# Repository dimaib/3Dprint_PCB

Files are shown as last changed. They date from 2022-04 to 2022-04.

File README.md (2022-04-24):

# 3D printer Dual
## Description
A board for controlling all parts of a dual-extruder 3D printer.
- Allows you to control 6 stepper motors
- Table heating 110-230V
- Chamber heating 110-230V
- Heat control of two extruders
- Connection of various limit switches
- Connecting the LCD display
- Printer management via web interface via TCP/IP
>This board is controlled by [RepRapFirmware](https://reprap.org/wiki/RepRap_Firmware) ([GitHub](https://github.com/reprappro/RepRapFirmware))

RepRapFirmware has been optimized and redesigned for the STM32F407VGT controller architecture

## Tools and softwire
- The printed circuit board and circuit diagram of the device are created in [KiCad](https://www.kicad.org/)
- 3D models for PCB components were created in SOLIDWORKS
- Firmware edit in [Atollic TrueSTUDIO for STM32](https://www.st.com/en/development-tools/truestudio.html) in C languages
## Main view PCB
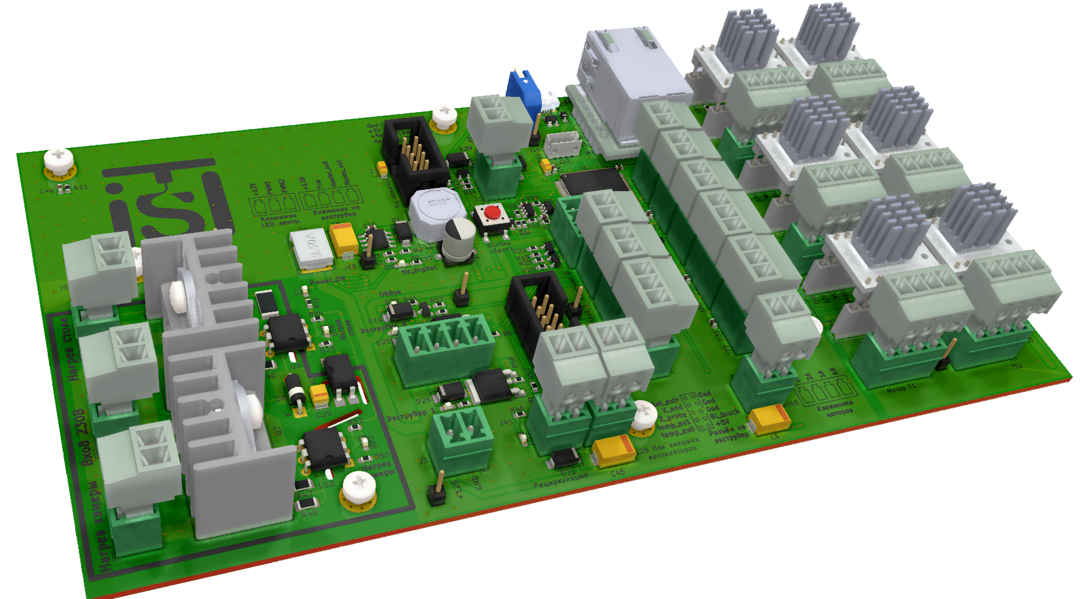
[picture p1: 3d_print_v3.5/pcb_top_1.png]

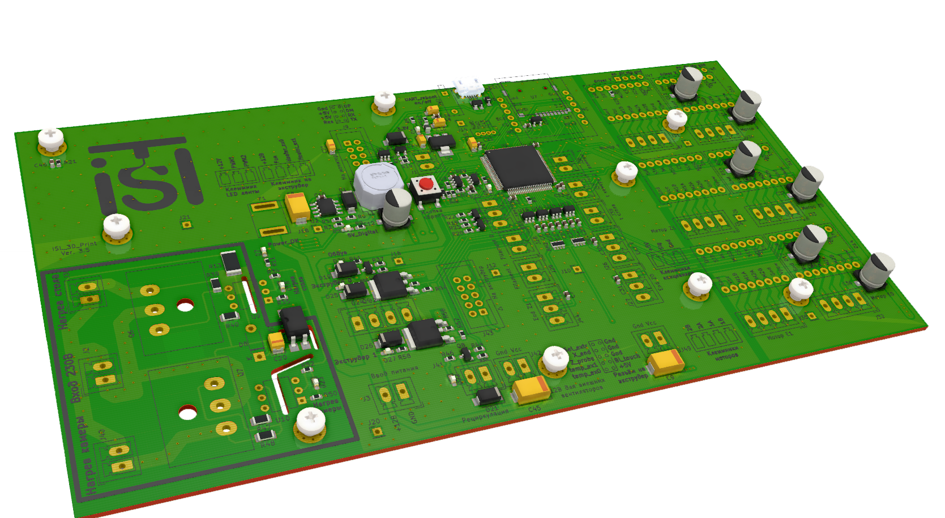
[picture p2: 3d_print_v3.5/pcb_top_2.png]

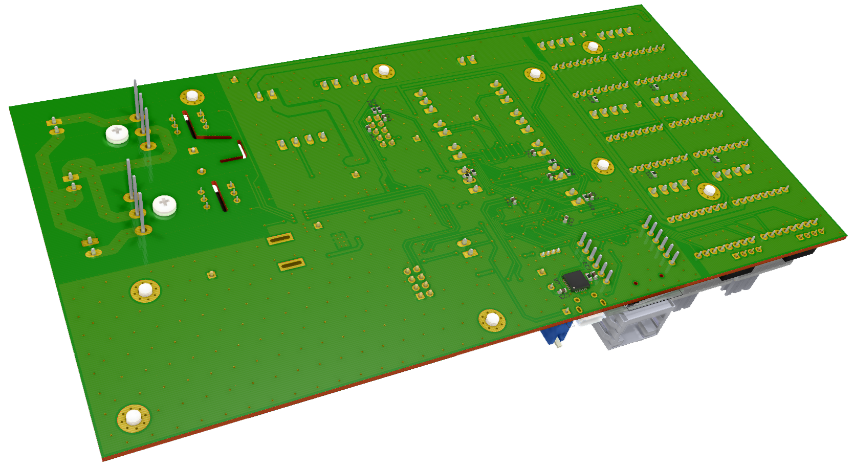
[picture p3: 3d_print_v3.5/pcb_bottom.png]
bottom


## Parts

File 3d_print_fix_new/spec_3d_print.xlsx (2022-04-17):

Спецификация платы принтера
На схеме | Значение | Ссылка | Цена шт | Кол-во | Цена общ
> C1, C2 | 2.2uF | https://www.chipdip.ru/product/grm188r61a225k | 6.00 ₽ | 2 | 12.00 ₽
> C3, C12 | 0.01uF | https://www.chipdip.ru/product0/9000143994 | 3.00 ₽ | 2 | 6.00 ₽
> C4, C10 | 1uF | https://www.chipdip.ru/product0/19661 | 16.00 ₽ | 2 | 32.00 ₽
> C6, C13 | 10uF | https://www.chipdip.ru/product0/634409749 | 29.00 ₽ | 2 | 58.00 ₽
> C8, C9, C26 | 10uF | https://www.chipdip.ru/product0/868717967 | 16.00 ₽ | 3 | 48.00 ₽
> C7, C14 | 220uF | https://www.chipdip.ru/product0/9000565740 | 10.00 ₽ | 2 | 20.00 ₽
> C15, C16 | 20pF | https://www.chipdip.ru/product0/472852716 | 6.00 ₽ | 2 | 12.00 ₽
C19 | 47uF 400V | https://www.chipdip.ru/product0/9000565879 | 46.00 ₽ | 1 | 46.00 ₽
> C20, C21 | 1000pF | https://www.chipdip.ru/product/grm1885c1h102j | 3.00 ₽ | 2 | 6.00 ₽
> C22, C43 | 0.01uF | https://www.chipdip.ru/product/grm21br72e103k | 13.00 ₽ | 2 | 26.00 ₽
> C5, C11, C23, C27-C32 | 100nF | https://www.chipdip.ru/product/grm188r71c104ka01d | 2.00 ₽ | 9 | 18.00 ₽
> C24, C25, C33-C36 | 1uF | https://www.chipdip.ru/product/grm188f51c105z | 3.00 ₽ | 6 | 18.00 ₽
> C37-C42 | 100uF | https://www.chipdip.ru/product0/9000565736 | 10.00 ₽ | 6 | 60.00 ₽
> D1, D11, D12, D16, D17 | SS16 | https://www.chipdip.ru/product/ss16 | 6.00 ₽ | 5 | 30.00 ₽
> D2, D3 | B340 | https://www.chipdip.ru/product/b340a-e3-61t-2 | 15.00 ₽ | 2 | 30.00 ₽
D4 | 1N4004 | https://www.chipdip.ru/product/1n4004-4 | 4.00 ₽ | 1 | 4.00 ₽
D5 | LED | https://www.chipdip.ru/product/to-1608bc-bf | 7.00 ₽ | 1 | 7.00 ₽
> D6-D8 | LED | https://www.chipdip.ru/product/to-1608bc-pg | 7.00 ₽ | 3 | 21.00 ₽
> D9, D10, D13, D26 | LED | https://www.chipdip.ru/product/to-1608bc-mre | 7.00 ₽ | 4 | 28.00 ₽
> D14, D15 | LED | https://www.chipdip.ru/product/to-1608bc-myf | 7.00 ₽ | 2 | 14.00 ₽
D18 | BAS321 | https://www.chipdip.ru/product/bas321.115 | 11.00 ₽ | 1 | 11.00 ₽
D19 | SP0503 | https://www.chipdip.ru/product/sp0503bahtg | 58.00 ₽ | 1 | 58.00 ₽
F1 | Fuse | https://www.chipdip.ru/product/mf-sm250 | 35.00 ₽ | 1 | 35.00 ₽
J1 | Температура стола | https://www.chipdip.ru/product/kls2-edv-3.50-02p-4-15edgvc-3.5-02p | 11.00 ₽ | 1 | 11.00 ₽
J2 | Температура камеры 1 | https://www.chipdip.ru/product/kls2-edv-3.50-02p-4-15edgvc-3.5-02p | 11.00 ₽ | 1 | 11.00 ₽
J3 | Разъём нагрева | https://www.chipdip.ru/product/idc-20ms | 13.00 ₽ | 1 | 13.00 ₽
J4 | USB_B_Mini | https://www.chipdip.ru/product/usb-m-1j | 30.00 ₽ | 1 | 30.00 ₽
J5 | Разъём для монитора | https://www.chipdip.ru/product/ds1014-12-mf1bxt-bhs2-12 | 8.00 ₽ | 1 | 8.00 ₽
J6 | ST-Link debug | https://www.chipdip.ru/product/b5b-xh-a | 30.00 ₽ | 1 | 30.00 ₽
J7 | Сброс! | https://www.chipdip.ru/product/kls2-edv-3.50-02p-4-15edgvc-3.5-02p | 11.00 ₽ | 1 | 11.00 ₽
J8 | Y концевик | https://www.chipdip.ru/product/15edgvc-3.5-03 | 7.00 ₽ | 1 | 7.00 ₽
J9 | Z концевик | https://www.chipdip.ru/product/15edgvc-3.5-03 | 7.00 ₽ | 1 | 7.00 ₽
J10 | Окончание пластика 0 | https://www.chipdip.ru/product/15edgvc-3.5-03 | 7.00 ₽ | 1 | 7.00 ₽
J11 | Окончание пластика 1 | https://www.chipdip.ru/product/15edgvc-3.5-03 | 7.00 ₽ | 1 | 7.00 ₽
J12 | Подключение RGB ленты | https://www.chipdip.ru/product/15edgvc-3.5-04 | 10.00 ₽ | 1 | 10.00 ₽
J13 | Conn_01x01 | https://www.chipdip.ru/product/pbs-7 | 8.00 ₽ | 1 | 8.00 ₽
J14 | Подключение двигателя X | https://www.chipdip.ru/product/15edgvc-3.5-04 | 10.00 ₽ | 1 | 10.00 ₽
J15 | Подключение двигателя Z0 | https://www.chipdip.ru/product/15edgvc-3.5-04 | 10.00 ₽ | 1 | 10.00 ₽
J16 | Подключение двигателя Y | https://www.chipdip.ru/product/15edgvc-3.5-04 | 10.00 ₽ | 1 | 10.00 ₽
J17 | Подключение двигателя Z1 | https://www.chipdip.ru/product/15edgvc-3.5-04 | 10.00 ₽ | 1 | 10.00 ₽
J18 | Подключение двигателя E0 | https://www.chipdip.ru/product/15edgvc-3.5-04 | 10.00 ₽ | 1 | 10.00 ₽
J19 | Подключение двигателя E1 | https://www.chipdip.ru/product/15edgvc-3.5-04 | 10.00 ₽ | 1 | 10.00 ₽
J20 | Питание стола | https://www.chipdip.ru/product/kls2-edv-3.50-02p-4-15edgvc-3.5-02p | 11.00 ₽ | 1 | 11.00 ₽
J21 | Температура камеры 2 | https://www.chipdip.ru/product/kls2-edv-3.50-02p-4-15edgvc-3.5-02p | 11.00 ₽ | 1 | 11.00 ₽
J22 | Вентилятор рециркуляции | https://www.chipdip.ru/product/kls2-edv-3.50-02p-4-15edgvc-3.5-02p | 11.00 ₽ | 1 | 11.00 ₽
J23 | Разъём экструдера | https://www.chipdip.ru/product/idc-16ms | 11.00 ₽ | 1 | 11.00 ₽
J24 | Нагрев стола | https://www.chipdip.ru/product/kls2-edv-3.50-02p-4-15edgvc-3.5-02p | 11.00 ₽ | 1 | 11.00 ₽
J25 | Нагрев камеры | https://www.chipdip.ru/product/kls2-edv-3.50-02p-4-15edgvc-3.5-02p | 11.00 ₽ | 1 | 11.00 ₽
J26 | Питание 12В | https://www.chipdip.ru/product/15edgvc-3.5-04 | 10.00 ₽ | 1 | 10.00 ₽
J27 | Conn_01x01 | https://www.chipdip.ru/product/pbs-8 | 10.00 ₽ | 6 | 60.00 ₽
J28 | Conn_01x01 | https://www.chipdip.ru/product/pbs-3 | 8.00 ₽ | 6 | 48.00 ₽
J29 | Conn_01x01 | https://www.chipdip.ru/product/pls-10-ds1021-1-10sf112 | 12.00 ₽ | 1 | 12.00 ₽
J30 | LMT01 - датчик т | https://www.chipdip.ru/product0/8002870711 | 94.00 ₽ | 3 | 282.00 ₽
> L1, L3 | 15uH | https://www.chipdip.ru/product/b82464g4153m | 80.00 ₽ | 2 | 160.00 ₽
L2 | 47uH | https://www.chipdip.ru/product/lqm21dn470n | 11.00 ₽ | 1 | 11.00 ₽
> Q1, Q2 | IRLR2905 | https://www.chipdip.ru/product/irlr2905trpbf-infineon | 46.00 ₽ | 2 | 92.00 ₽
> Q3, Q13 | BT139 | https://www.chipdip.ru/product/bt139-600 | 52.00 ₽ | 2 | 104.00 ₽
> Q4, Q5, Q8, Q12 | BC817 | https://www.chipdip.ru/product/bc817-16-nxp | 4.00 ₽ | 4 | 16.00 ₽
> Q6, Q7, Q9-Q11 | IRLML2060 | https://www.chipdip.ru/product/irlml2060trpbf | 12.00 ₽ | 5 | 60.00 ₽
> R3, R6 | 3k | https://www.chipdip.ru/product0/9000079723 | 2.00 ₽ | 2 | 4.00 ₽
> R4, R7 | 240 | https://www.chipdip.ru/product0/9000079601 | 2.00 ₽ | 2 | 4.00 ₽
R8 | 30k | https://www.chipdip.ru/product0/9000079449 | 2.00 ₽ | 1 | 2.00 ₽
> R1, R9, R22, R41, R60-R62, R64 | 360 | https://www.chipdip.ru/product0/9000079629 | 2.00 ₽ | 8 | 16.00 ₽
> R11, R19 | 100k | https://www.chipdip.ru/product0/9000079760 | 2.00 ₽ | 2 | 4.00 ₽
> R23, R63 | 380 | https://www.chipdip.ru/product0/9000079711 | 2.00 ₽ | 2 | 4.00 ₽
> R24, R65 | 39 | https://www.chipdip.ru/product0/9000079881 | 2.00 ₽ | 2 | 4.00 ₽
> R25, R66 | 330 | https://www.chipdip.ru/product0/9000079709 | 2.00 ₽ | 2 | 4.00 ₽
> R2, R5, R12, R13, R16, R17, R20, R21, R26-R31, R34, R35, R38, R42, R43, R45, R46, R48, R49, R57-R59, R67 | 10k | https://www.chipdip.ru/product0/9000079736 | 2.00 ₽ | 27 | 54.00 ₽
> R36, R37 | 4.7k | https://www.chipdip.ru/product0/9000079728 | 2.00 ₽ | 2 | 4.00 ₽
> R39, R40 | 22 | https://www.chipdip.ru/product0/9000079564 | 2.00 ₽ | 2 | 4.00 ₽
> R10, R14, R15, R18, R32, R33, R44, R47, R56 | 100 | https://www.chipdip.ru/product0/9000079616 | 2.00 ₽ | 9 | 18.00 ₽
> RN2, RN4 | 4.7k | https://www.chipdip.ru/product/cat16-472j4 | 3.00 ₽ | 2 | 6.00 ₽
> RN3, RN5 | 1k | https://www.chipdip.ru/product/cat16-102j4 | 3.00 ₽ | 2 | 6.00 ₽
SW1 | Сброс принтера | https://www.chipdip.ru/product/kls7-ts6604-4.3-180-b-it-1102s | 8.00 ₽ | 1 | 8.00 ₽
U1 | STM32F407VGTx | https://www.chipdip.ru/product0/8001812222 | 490.00 ₽ | 1 | 490.00 ₽
U2 | AZ1117-3.3 | https://www.chipdip.ru/product1/8001925229 | 4.00 ₽ | 1 | 4.00 ₽
> U3, U4 | TPS5430DDA | https://www.chipdip.ru/product/tps5430ddar | 160.00 ₽ | 2 | 320.00 ₽
U5 | LTV-817S | https://www.chipdip.ru/product0/8001777801 | 9.00 ₽ | 1 | 9.00 ₽
> U6, U7 | INA333 | https://www.chipdip.ru/product0/8002871657 | 210.00 ₽ | 2 | 420.00 ₽
> U8, U12 | MOC3041M | https://www.chipdip.ru/product/moc3041m | 34.00 ₽ | 2 | 68.00 ₽
U9 | AT24C256 | https://www.chipdip.ru/product/at24c256c-sshl-t | 34.00 ₽ | 1 | 34.00 ₽
U10 | USBLC6-2SC6 | https://www.chipdip.ru/product/usblc6-2sc6 | 10.00 ₽ | 1 | 10.00 ₽
U11 | CP2102N | https://www.chipdip.ru/product/cp2102-gmr | 140.00 ₽ | 1 | 140.00 ₽
U13 | MicroSD_SPI_CD | https://www.chipdip.ru/product0/8001774160 | 84.00 ₽ | 1 | 84.00 ₽
Y1 | 8MHz | https://www.chipdip.ru/product0/9000523954 | 19.00 ₽ | 1 | 19.00 ₽
Y2 | 32.768KHz | https://www.chipdip.ru/product0/9000372611 | 45.00 ₽ | 1 | 45.00 ₽

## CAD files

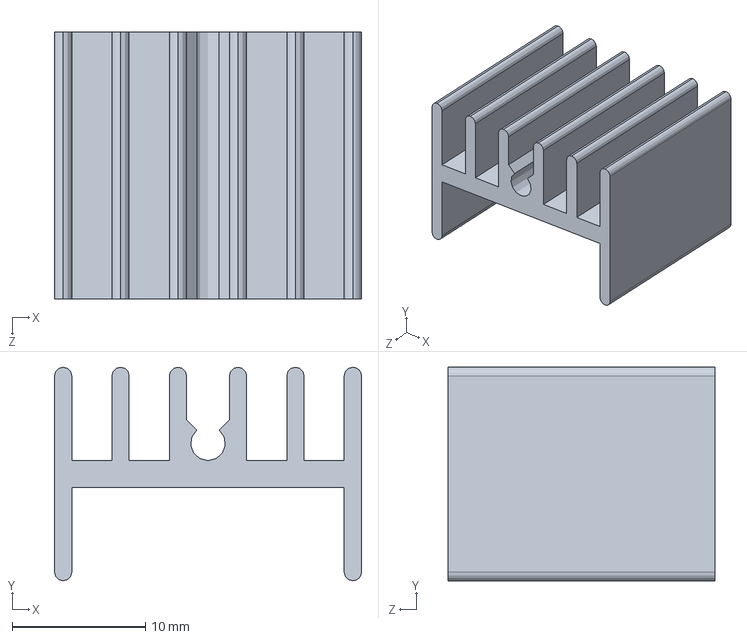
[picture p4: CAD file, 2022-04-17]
3d_print_fix_new/shapes3D/radiator2.SLDPRT
23.0 x 16.0 x 20.0 mm

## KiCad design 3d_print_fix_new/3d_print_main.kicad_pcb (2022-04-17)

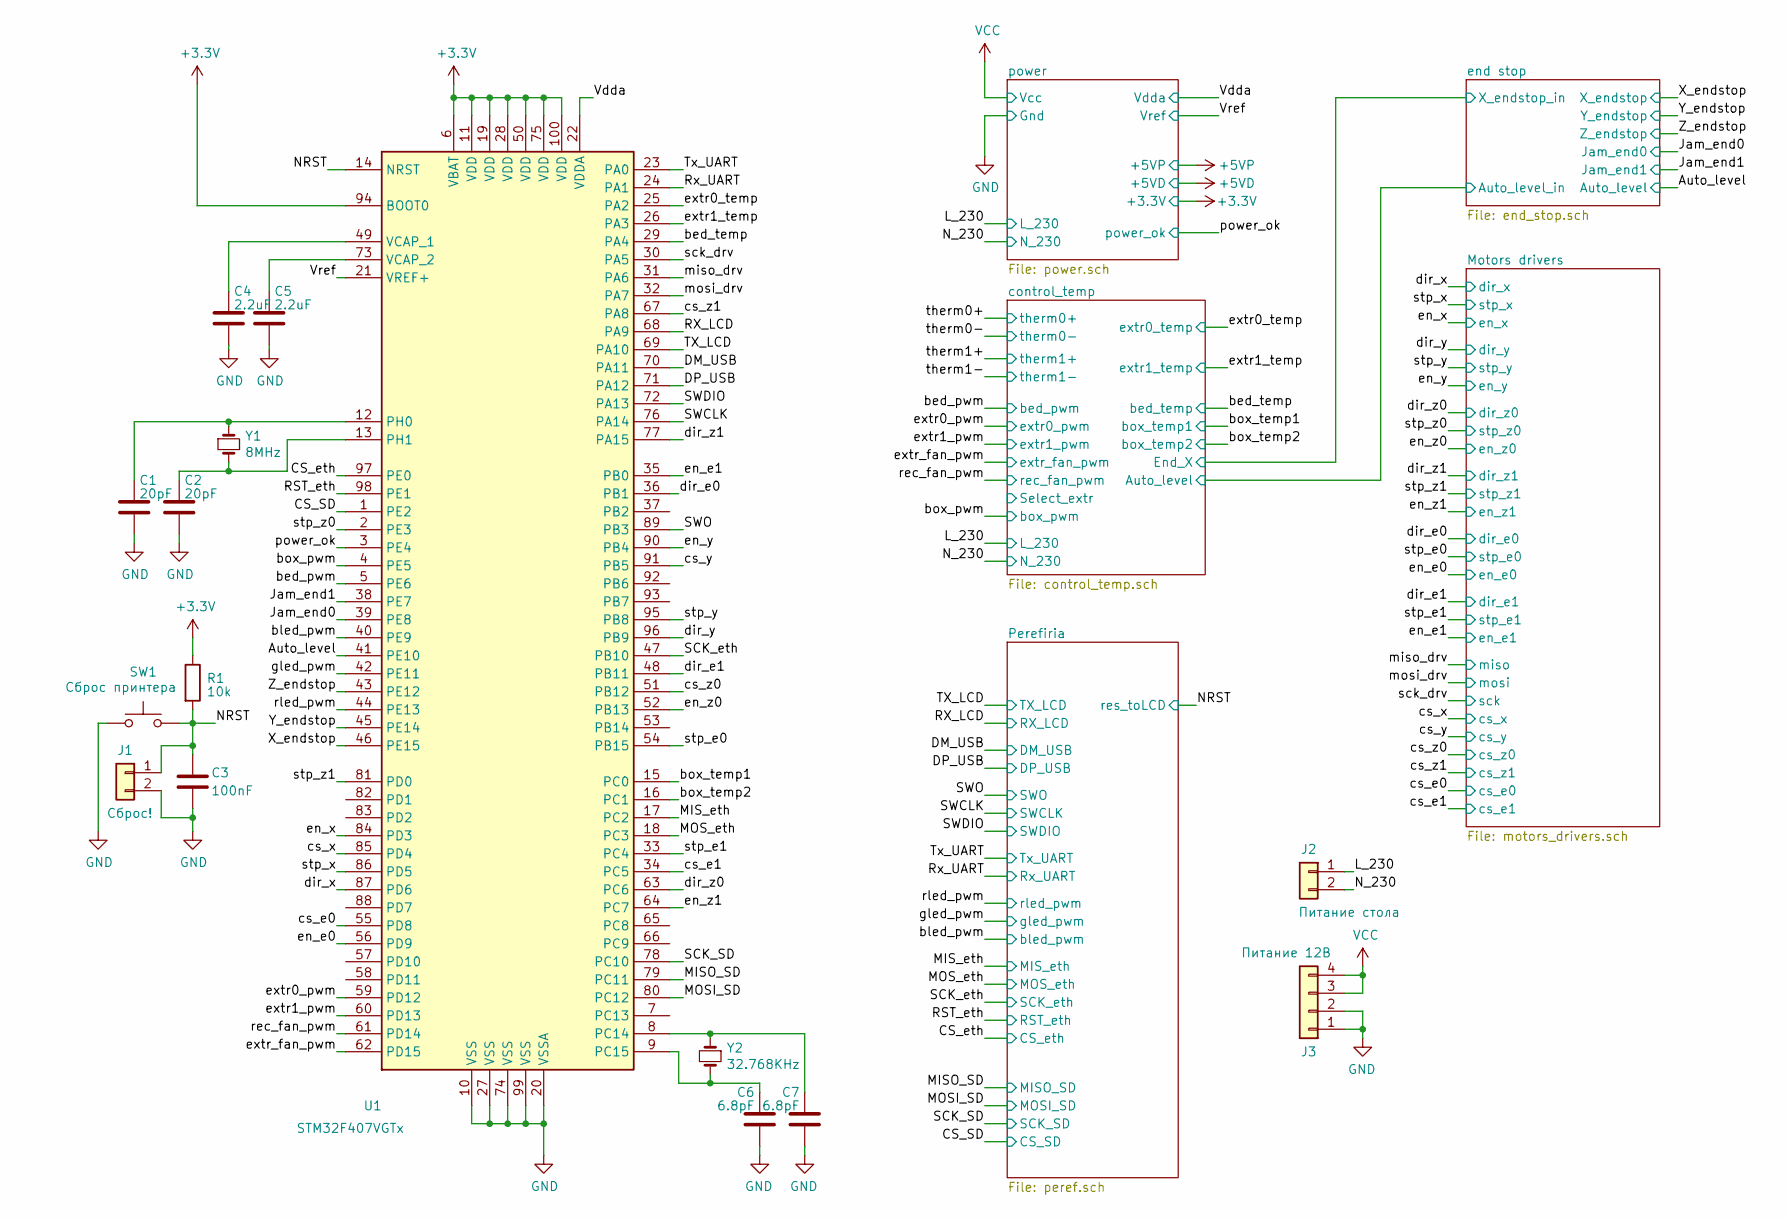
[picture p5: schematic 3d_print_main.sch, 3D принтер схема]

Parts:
C1, C2: 20pF; C_0603_1608Metric
C3: 100nF; C_0603_1608Metric
C4, C5: 2.2uF; C_0603_1608Metric
C6, C7: 6.8pF; C_0603_1608Metric
J1: Сброс!; PhoenixContact_MCV_1,5_2-G-3.5_1x02_P3.50mm_Vertical
J2: Питание стола; PhoenixContact_MCV_1,5_2-G-3.5_1x02_P3.50mm_Vertical
J3: Питание 12В; PhoenixContact_MCV_1,5_4-G-3.5_1x04_P3.50mm_Vertical
R1: 10k; R_0603_1608Metric
SW1: Сброс принтера; SW_SPST_PTS645
U1: STM32F407VGTx; LQFP-100_14x14mm_P0.5mm
Y1: 8MHz; Crystal_SMD_5032-2Pin_5.0x3.2mm_HandSoldering
Y2: 32.768KHz; Crystal_SMD_3215-2Pin_3.2x1.5mm

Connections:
+3V3: R1.1, U1.6 (VBAT), U1.11 (VDD), U1.19 (VDD), U1.28 (VDD), U1.50 (VDD), U1.75 (VDD), U1.94 (BOOT0), U1.100 (VDD); also elsewhere on the board
/Auto_level: U1.41 (PE10); also elsewhere on the board
/CS_SD: U1.1 (PE2); also elsewhere on the board
/CS_eth: U1.97 (PE0); also elsewhere on the board
/DM_USB: U1.70 (PA11); also elsewhere on the board
/DP_USB: U1.71 (PA12); also elsewhere on the board
/Jam_end0: U1.39 (PE8); also elsewhere on the board
/Jam_end1: U1.38 (PE7); also elsewhere on the board
/L_230: J2.1; also elsewhere on the board
/MISO_SD: U1.79 (PC11); also elsewhere on the board
/MIS_eth: U1.17 (PC2); also elsewhere on the board
/MOSI_SD: U1.80 (PC12); also elsewhere on the board
/MOS_eth: U1.18 (PC3); also elsewhere on the board
/NRST: C3.1, J1.1, R1.2, SW1.2, U1.14 (NRST); also elsewhere on the board
/N_230: J2.2; also elsewhere on the board
/RST_eth: U1.98 (PE1); also elsewhere on the board
/RX_LCD: U1.68 (PA9); also elsewhere on the board
/Rx_UART: U1.24 (PA1); also elsewhere on the board
/SCK_SD: U1.78 (PC10); also elsewhere on the board
/SCK_eth: U1.47 (PB10); also elsewhere on the board
/SWCLK: U1.76 (PA14); also elsewhere on the board
/SWDIO: U1.72 (PA13); also elsewhere on the board
/SWO: U1.89 (PB3); also elsewhere on the board
/TX_LCD: U1.69 (PA10); also elsewhere on the board
/Tx_UART: U1.23 (PA0); also elsewhere on the board
/Vdda: U1.22 (VDDA); also elsewhere on the board
/Vref: U1.21 (VREF+); also elsewhere on the board
/X_endstop: U1.46 (PE15); also elsewhere on the board
/Y_endstop: U1.45 (PE14); also elsewhere on the board
/Z_endstop: U1.43 (PE12); also elsewhere on the board
/bed_pwm: U1.5 (PE6); also elsewhere on the board
/bed_temp: U1.29 (PA4); also elsewhere on the board
/bled_pwm: U1.40 (PE9); also elsewhere on the board
/box_pwm: U1.4 (PE5); also elsewhere on the board
/box_temp1: U1.15 (PC0); also elsewhere on the board
/box_temp2: U1.16 (PC1); also elsewhere on the board
/cs_e0: U1.55 (PD8); also elsewhere on the board
/cs_e1: U1.34 (PC5); also elsewhere on the board
/cs_x: U1.85 (PD4); also elsewhere on the board
/cs_y: U1.91 (PB5); also elsewhere on the board
/cs_z0: U1.51 (PB12); also elsewhere on the board
/cs_z1: U1.67 (PA8); also elsewhere on the board
/dir_e0: U1.36 (PB1); also elsewhere on the board
/dir_e1: U1.48 (PB11); also elsewhere on the board
/dir_x: U1.87 (PD6); also elsewhere on the board
/dir_y: U1.96 (PB9); also elsewhere on the board
/dir_z0: U1.63 (PC6); also elsewhere on the board
/dir_z1: U1.77 (PA15); also elsewhere on the board
/en_e0: U1.56 (PD9); also elsewhere on the board
/en_e1: U1.35 (PB0); also elsewhere on the board
/en_x: U1.84 (PD3); also elsewhere on the board
/en_y: U1.90 (PB4); also elsewhere on the board
/en_z0: U1.52 (PB13); also elsewhere on the board
/en_z1: U1.64 (PC7); also elsewhere on the board
/extr0_pwm: U1.59 (PD12); also elsewhere on the board
/extr0_temp: U1.25 (PA2); also elsewhere on the board
/extr1_pwm: U1.60 (PD13); also elsewhere on the board
/extr1_temp: U1.26 (PA3); also elsewhere on the board
/extr_fan_pwm: U1.62 (PD15); also elsewhere on the board
/gled_pwm: U1.42 (PE11); also elsewhere on the board
/miso_drv: U1.31 (PA6); also elsewhere on the board
/mosi_drv: U1.32 (PA7); also elsewhere on the board
/power_ok: U1.3 (PE4); also elsewhere on the board
/rec_fan_pwm: U1.61 (PD14); also elsewhere on the board
/rled_pwm: U1.44 (PE13); also elsewhere on the board
/sck_drv: U1.30 (PA5); also elsewhere on the board
/stp_e0: U1.54 (PB15); also elsewhere on the board
/stp_e1: U1.33 (PC4); also elsewhere on the board
/stp_x: U1.86 (PD5); also elsewhere on the board
/stp_y: U1.95 (PB8); also elsewhere on the board
/stp_z0: U1.2 (PE3); also elsewhere on the board
/stp_z1: U1.81 (PD0); also elsewhere on the board
GND: C1.2, C2.2, C3.2, C4.2, C5.2, C6.2, C7.2, J1.2, J3.1, J3.2, SW1.1, U1.10 (VSS), U1.20 (VSSA), U1.27 (VSS), U1.74 (VSS), U1.99 (VSS); also elsewhere on the board
unnamed: C1.1, U1.12 (PH0), Y1.1
unnamed: C2.1, U1.13 (PH1), Y1.2
unnamed: C4.1, U1.49 (VCAP_1)
unnamed: C5.1, U1.73 (VCAP_2)
unnamed: C6.1, U1.9 (PC15), Y2.2
unnamed: C7.1, U1.8 (PC14), Y2.1
VCC: J3.3, J3.4; also elsewhere on the board

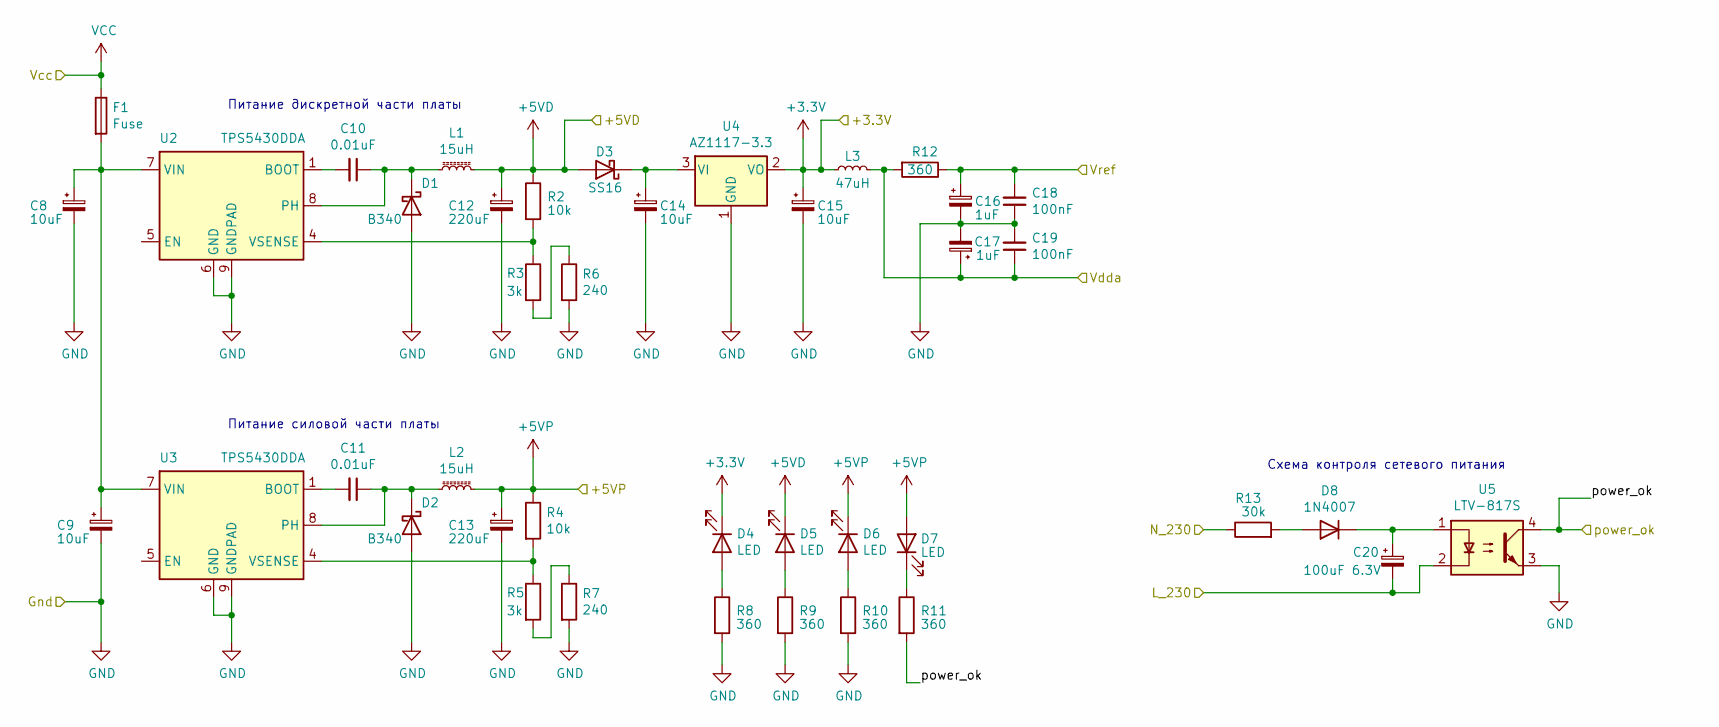
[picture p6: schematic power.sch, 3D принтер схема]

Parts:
C8, C9: 10uF; CP_EIA-6032-28_Kemet-C
C10, C11: 0.01uF; C_0603_1608Metric
C12, C13: 220uF; CP_Elec_6.3x7.7
C14, C15: 10uF; CP_EIA-3216-18_Kemet-A
C16, C17: 1uF; CP_EIA-3216-18_Kemet-A
C18, C19: 100nF; C_0603_1608Metric
C20: 100uF 6.3V; CP_EIA-3528-21_Kemet-B
D1, D2: B340; D_SMA
D3: SS16; D_SMA
D4, D5, D6, D7: LED; LED_1206_3216Metric
D8: 1N4007; D_DO-41_SOD81_P7.62mm_Horizontal
F1: Fuse; MF-SM250_Fuse
L1, L2: 15uH; L_10.4x10.4_H4.8
L3: 47uH; L_0805_2012Metric
R2, R4: 10k; R_0603_1608Metric
R3, R5: 3k; R_0603_1608Metric
R6, R7: 240; R_0603_1608Metric
R8, R9, R10, R11, R12: 360; R_0603_1608Metric
R13: 30k; R_2512_6332Metric
U2, U3: TPS5430DDA; TI_SO-PowerPAD-8_ThermalVias
U4: AZ1117-3.3; SOT-223-3_TabPin2
U5: LTV-817S; SMDIP-4_W9.53mm

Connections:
+3V3: C15.1, D4.1 (K), L3.1, U4.2 (VO); also elsewhere on the board
+5VD: C12.1, D3.2 (A), D5.1 (K), L1.2, R2.1; also elsewhere on the board
+5VP: C13.1, D6.1 (K), D7.2 (A), L2.2, R4.1; also elsewhere on the board
/L_230: C20.2, U5.2; also elsewhere on the board
/N_230: R13.1; also elsewhere on the board
/Vdda: C17.1, C19.1, L3.2, R12.2; also elsewhere on the board
/Vref: C16.1, C18.2, R12.1; also elsewhere on the board
/power_ok: R11.2, U5.4; also elsewhere on the board
GND: C8.2, C9.2, C12.2, C13.2, C14.2, C15.2, C16.2, C17.2, C18.1, C19.2, D1.2 (A), D2.2 (A), R6.2, R7.2, R8.2, R9.2, R10.2, U2.6 (GND), U2.9 (GNDPAD), U3.6 (GND), U3.9 (GNDPAD), U4.1 (GND), U5.3; also elsewhere on the board
unnamed: C8.1, C9.1, F1.2, U2.7 (VIN), U3.7 (VIN)
unnamed: C10.1, D1.1 (K), L1.1, U2.8 (PH)
unnamed: C10.2, U2.1 (BOOT)
unnamed: C11.1, D2.1 (K), L2.1, U3.8 (PH)
unnamed: C11.2, U3.1 (BOOT)
unnamed: C14.1, D3.1 (K), U4.3 (VI)
unnamed: C20.1, D8.2 (K), U5.1
unnamed: D4.2 (A), R8.1
unnamed: D5.2 (A), R9.1
unnamed: D6.2 (A), R10.1
unnamed: D7.1 (K), R11.1
unnamed: D8.1 (A), R13.2
unnamed: R2.2, R3.1, U2.4 (VSENSE)
unnamed: R3.2, R6.1
unnamed: R4.2, R5.1, U3.4 (VSENSE)
unnamed: R5.2, R7.1
VCC: F1.1; also elsewhere on the board

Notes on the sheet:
Питание дискретной части платы
Питание силовой части платы
Схема контроля сетевого питания

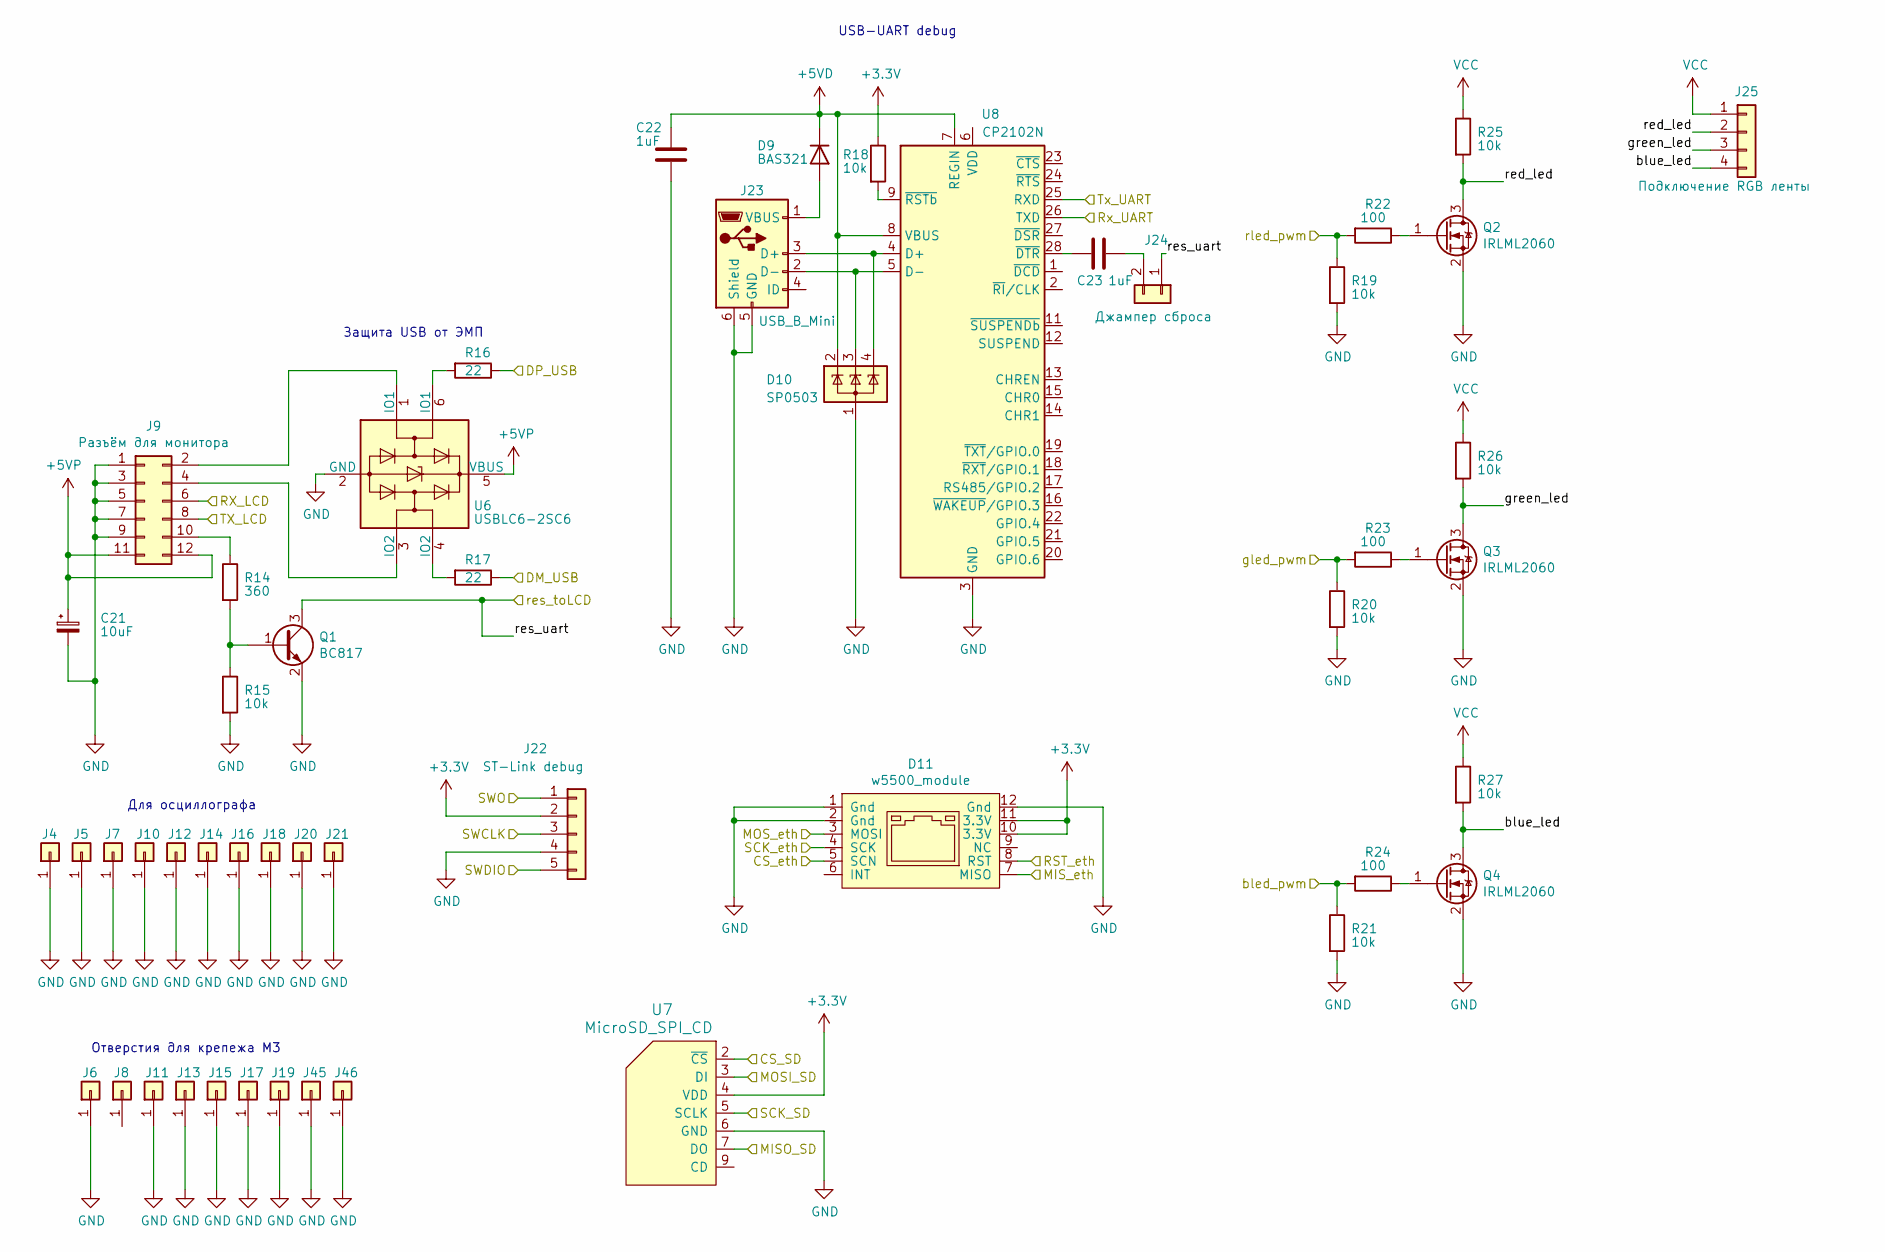
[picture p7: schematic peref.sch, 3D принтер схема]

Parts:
C21: 10uF; CP_EIA-3216-18_Kemet-A
C22, C23: 1uF; C_0603_1608Metric
D9: BAS321; D_SOD-323_HandSoldering
D10: SP0503; SOT-143
D11: w5500_module
J4, J5, J7, J12, J14, J16, J18, J20, J21: Conn_01x01; PinHeader_1x01_P2.54mm_Vertical
J6, J8, J11, J13, J15, J17, J19, J45, J46: Conn_01x01; MountingHole_3.2mm_M3_Pad_Via
J9: Разъём для монитора; IDC-Header_2x06_P2.54mm_Vertical
J10: LMT01 датчик т; PinHeader_1x01_P2.54mm_Vertical
J22: ST-Link debug; JST_XH_B5B-XH-A_1x05_P2.50mm_Vertical
J23: USB_B_Mini; USB_Mini-B_Lumberg_2486_01_Horizontal
J24: Джампер сброса; PinHeader_1x02_P2.54mm_Vertical
J25: Подключение RGB ленты; PhoenixContact_MCV_1,5_4-G-3.5_1x04_P3.50mm_Vertical
Q1: BC817; SOT-23
Q2, Q3, Q4: IRLML2060; SOT-23
R14: 360; R_0603_1608Metric
R15, R18, R19, R20, R21, R25, R26, R27: 10k; R_0603_1608Metric
R16, R17: 22; R_0603_1608Metric
R22, R23, R24: 100; R_0603_1608Metric
U6: USBLC6-2SC6; SOT-23-6
U7: MicroSD_SPI_CD; GCT-MEM2055-00-190-01-A
U8: CP2102N; QFN-28-1EP_5x5mm_P0.5mm_EP3.35x3.35mm

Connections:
+3V3: D11.10 (3.3V), D11.11 (3.3V), J22.2, R18.1, U7.4 (VDD); also elsewhere on the board
+5VD: C22.1, D9.2 (K), D10.2 (K), U8.7 (REGIN), U8.8 (VBUS); also elsewhere on the board
+5VP: C21.1, J9.11, J9.12, U6.5 (VBUS); also elsewhere on the board
/CS_SD: U7.2 (~CS); also elsewhere on the board
/CS_eth: D11.5 (SCN); also elsewhere on the board
/DM_USB: R17.1; also elsewhere on the board
/DP_USB: R16.1; also elsewhere on the board
/MISO_SD: U7.7 (DO); also elsewhere on the board
/MIS_eth: D11.7 (MISO); also elsewhere on the board
/MOSI_SD: U7.3 (DI); also elsewhere on the board
/MOS_eth: D11.3 (MOSI); also elsewhere on the board
/NRST: J24.1, Q1.3 (C); also elsewhere on the board
/Perefiria/blue_led: J25.4, Q4.3 (D), R27.2
/Perefiria/green_led: J25.3, Q3.3 (D), R26.2
/Perefiria/red_led: J25.2, Q2.3 (D), R25.2
/RST_eth: D11.8 (RST); also elsewhere on the board
/RX_LCD: J9.6; also elsewhere on the board
/Rx_UART: U8.26 (TXD); also elsewhere on the board
/SCK_SD: U7.5 (SCLK); also elsewhere on the board
/SCK_eth: D11.4 (SCK); also elsewhere on the board
/SWCLK: J22.3; also elsewhere on the board
/SWDIO: J22.5; also elsewhere on the board
/SWO: J22.1; also elsewhere on the board
/TX_LCD: J9.8; also elsewhere on the board
/Tx_UART: U8.25 (RXD); also elsewhere on the board
/bled_pwm: R21.1, R24.2; also elsewhere on the board
/gled_pwm: R20.1, R23.2; also elsewhere on the board
/rled_pwm: R19.1, R22.2; also elsewhere on the board
GND: C21.2, C22.2, D10.1 (A), D11.1 (Gnd), D11.2 (Gnd), D11.12 (Gnd), J4.1, J5.1, J6.1, J7.1, J9.1, J9.3, J9.5, J9.7, J9.9, J10.1, J11.1, J12.1, J13.1, J14.1, J15.1, J16.1, J17.1, J18.1, J19.1, J20.1, J21.1, J22.4, J23.5 (GND), J23.6 (Shield), J45.1, J46.1, Q1.2 (E), Q2.2 (S), Q3.2 (S), Q4.2 (S), R15.2, R19.2, R20.2, R21.2, U6.2 (GND), U7.6 (GND), U8.3 (GND), U8.29 (GND); also elsewhere on the board
unnamed: C23.1, J24.2
unnamed: C23.2, U8.28 (~DTR)
unnamed: D9.1 (A), J23.1 (VBUS)
unnamed: D10.3 (K), J23.2 (D-), U8.5 (D-)
unnamed: D10.4 (K), J23.3 (D+), U8.4 (D+)
unnamed: J9.2, U6.1 (IO1)
unnamed: J9.4, U6.3 (IO2)
unnamed: J9.10, R14.1
unnamed: Q1.1 (B), R14.2, R15.1
unnamed: Q2.1 (G), R22.1
unnamed: Q3.1 (G), R23.1
unnamed: Q4.1 (G), R24.1
unnamed: R16.2, U6.6 (IO1)
unnamed: R17.2, U6.4 (IO2)
unnamed: R18.2, U8.9 (~RSTb)
VCC: J25.1, R25.1, R26.1, R27.1; also elsewhere on the board

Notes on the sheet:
USB-UART debug
Защита USB от ЭМП
Для осциллографа
Отверстия для крепежа M3

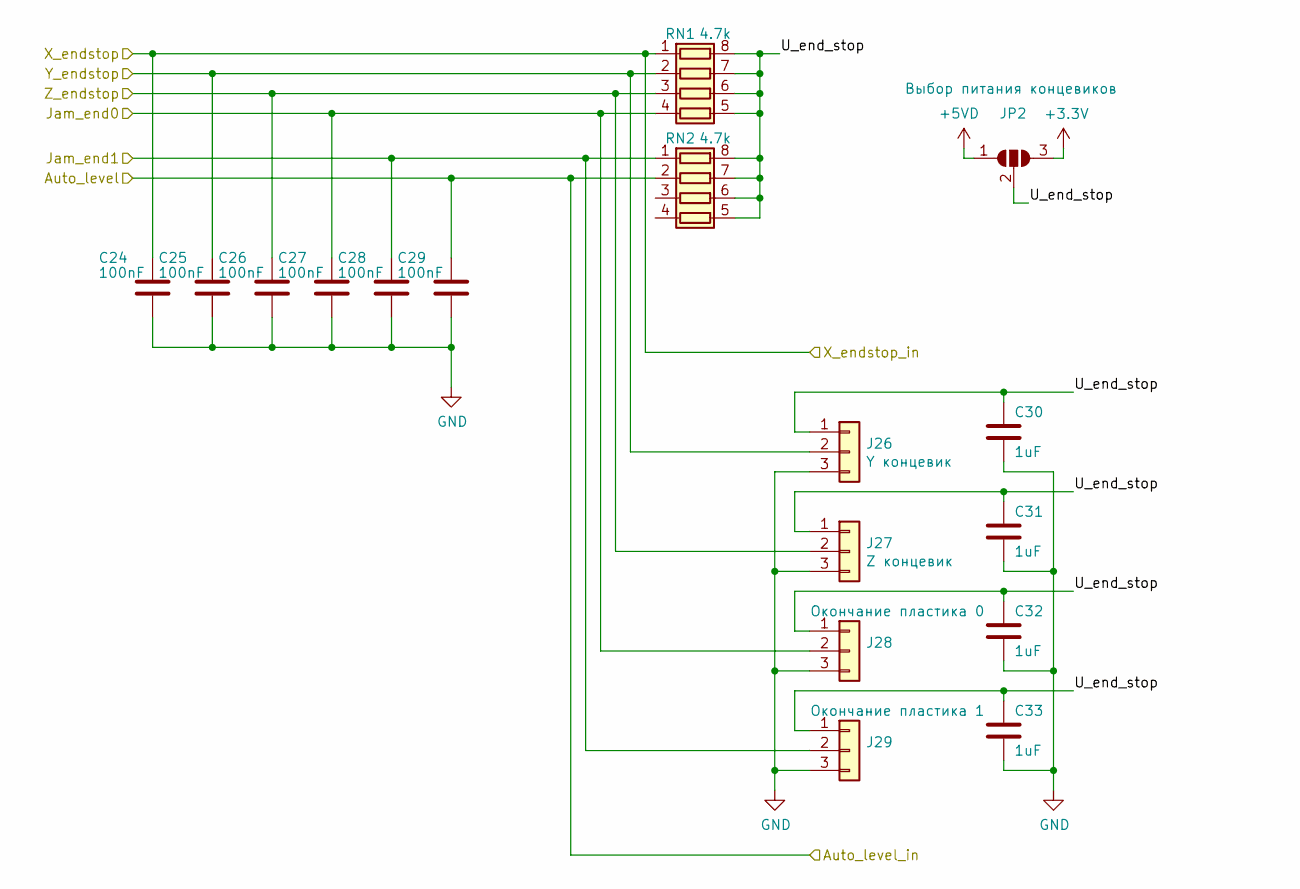
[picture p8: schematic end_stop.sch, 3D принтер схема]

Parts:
C24, C25, C26, C27, C28, C29: 100nF; C_0603_1608Metric
C30, C31, C32, C33: 1uF; C_0603_1608Metric
J26: Y концевик; PhoenixContact_MCV_1,5_3-G-3.5_1x03_P3.50mm_Vertical
J27: Z концевик; PhoenixContact_MCV_1,5_3-G-3.5_1x03_P3.50mm_Vertical
J28: Окончание пластика 0; PhoenixContact_MCV_1,5_3-G-3.5_1x03_P3.50mm_Vertical
J29: Окончание пластика 1; PhoenixContact_MCV_1,5_3-G-3.5_1x03_P3.50mm_Vertical
JP2: Выбор питания концевиков; SolderJumper-3_P1.3mm_Bridged2Bar12_RoundedPad1.0x1.5mm_Num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
RN1, RN2: 4.7k; R_Array_Convex_4x0603

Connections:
+3V3: JP2.3 (B); also elsewhere on the board
+5VD: JP2.1 (A); also elsewhere on the board
/Auto_level: C29.1, RN2.2 (R2.1); also elsewhere on the board
/Jam_end0: C27.1, J28.2, RN1.4 (R4.1); also elsewhere on the board
/Jam_end1: C28.1, J29.2, RN2.1 (R1.1); also elsewhere on the board
/X_endstop: C24.1, RN1.1 (R1.1); also elsewhere on the board
/Y_endstop: C25.1, J26.2, RN1.2 (R2.1); also elsewhere on the board
/Z_endstop: C26.1, J27.2, RN1.3 (R3.1); also elsewhere on the board
/end stop/U_end_stop: C30.1, C31.1, C32.1, C33.1, J26.1, J27.1, J28.1, J29.1, JP2.2 (C), RN1.5 (R4.2), RN1.6 (R3.2), RN1.7 (R2.2), RN1.8 (R1.2), RN2.5 (R4.2), RN2.6 (R3.2), RN2.7 (R2.2), RN2.8 (R1.2)
GND: C24.2, C25.2, C26.2, C27.2, C28.2, C29.2, C30.2, C31.2, C32.2, C33.2, J26.3, J27.3, J28.3, J29.3; also elsewhere on the board

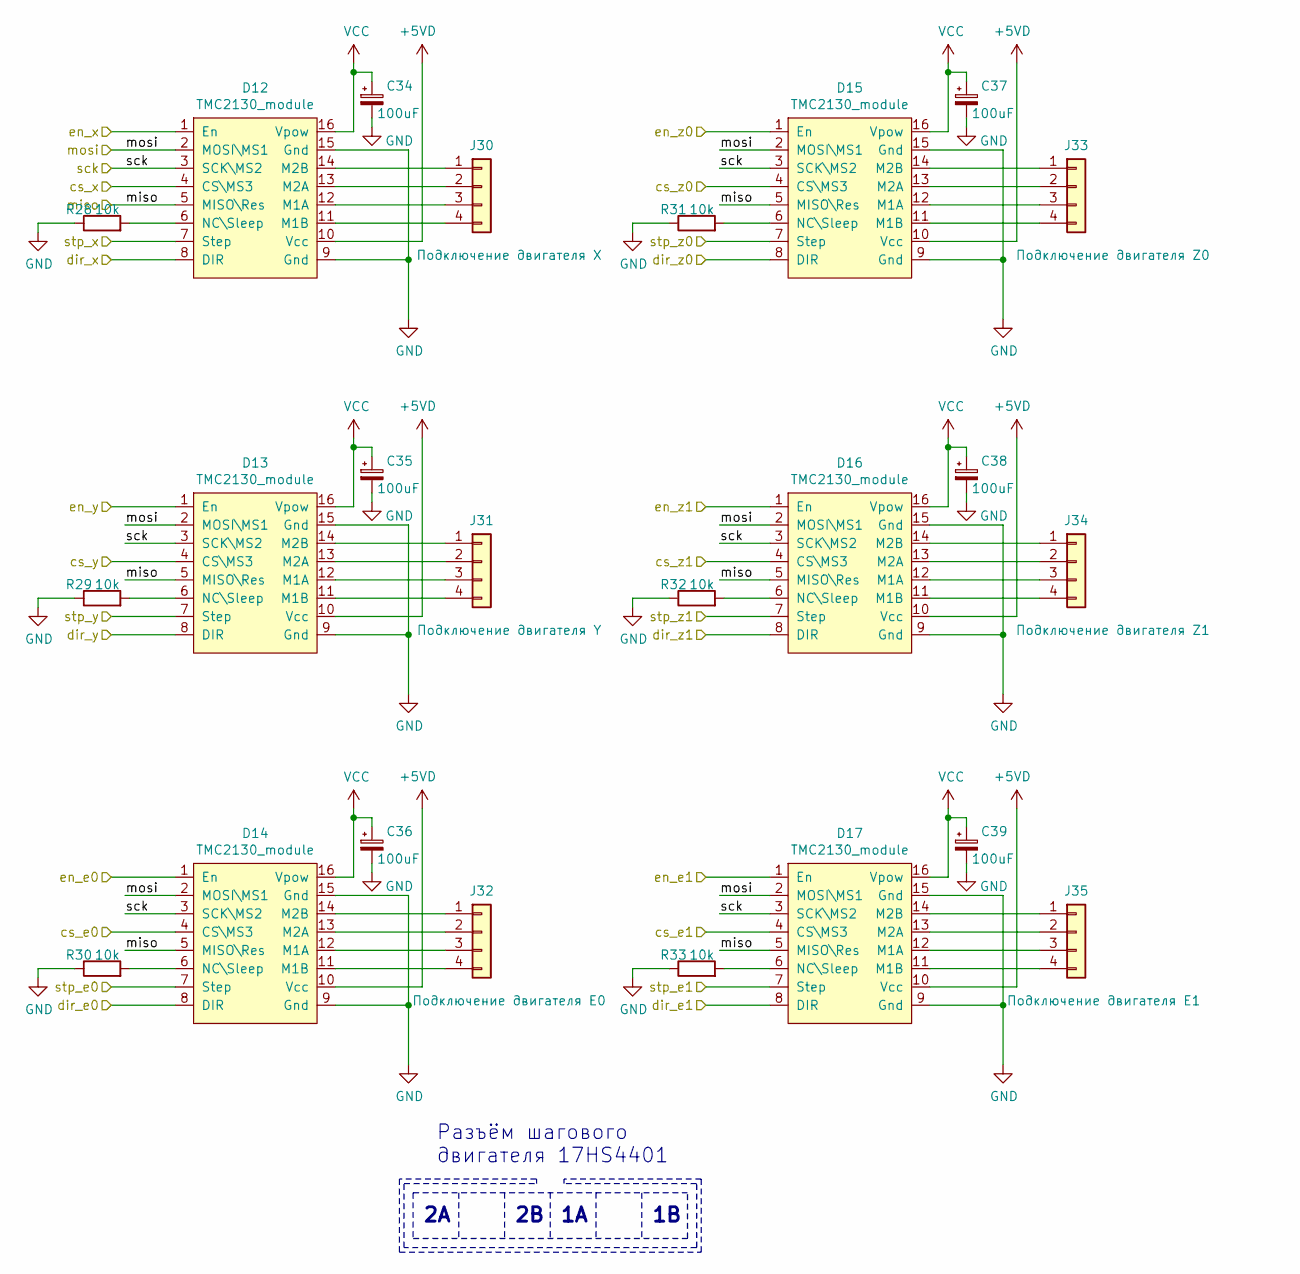
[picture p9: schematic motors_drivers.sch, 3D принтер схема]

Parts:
C34, C35, C36, C37, C38, C39: 100uF; CP_Elec_6.3x7.7
D12, D13, D14, D15, D16, D17: TMC2130_module; TMC2130_Module
J30: Подключение двигателя X; PhoenixContact_MCV_1,5_4-G-3.5_1x04_P3.50mm_Vertical
J31: Подключение двигателя Y; PhoenixContact_MCV_1,5_4-G-3.5_1x04_P3.50mm_Vertical
J32: Подключение двигателя E0; PhoenixContact_MCV_1,5_4-G-3.5_1x04_P3.50mm_Vertical
J33: Подключение двигателя Z0; PhoenixContact_MCV_1,5_4-G-3.5_1x04_P3.50mm_Vertical
J34: Подключение двигателя Z1; PhoenixContact_MCV_1,5_4-G-3.5_1x04_P3.50mm_Vertical
J35: Подключение двигателя E1; PhoenixContact_MCV_1,5_4-G-3.5_1x04_P3.50mm_Vertical
R28, R29, R30, R31, R32, R33: 10k; R_0603_1608Metric

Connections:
+5VD: D12.10 (Vcc), D13.10 (Vcc), D14.10 (Vcc), D15.10 (Vcc), D16.10 (Vcc), D17.10 (Vcc); also elsewhere on the board
/cs_e0: D14.4 (CS\MS3); also elsewhere on the board
/cs_e1: D17.4 (CS\MS3); also elsewhere on the board
/cs_x: D12.4 (CS\MS3); also elsewhere on the board
/cs_y: D13.4 (CS\MS3); also elsewhere on the board
/cs_z0: D15.4 (CS\MS3); also elsewhere on the board
/cs_z1: D16.4 (CS\MS3); also elsewhere on the board
/dir_e0: D14.8 (DIR); also elsewhere on the board
/dir_e1: D17.8 (DIR); also elsewhere on the board
/dir_x: D12.8 (DIR); also elsewhere on the board
/dir_y: D13.8 (DIR); also elsewhere on the board
/dir_z0: D15.8 (DIR); also elsewhere on the board
/dir_z1: D16.8 (DIR); also elsewhere on the board
/en_e0: D14.1 (En); also elsewhere on the board
/en_e1: D17.1 (En); also elsewhere on the board
/en_x: D12.1 (En); also elsewhere on the board
/en_y: D13.1 (En); also elsewhere on the board
/en_z0: D15.1 (En); also elsewhere on the board
/en_z1: D16.1 (En); also elsewhere on the board
/miso_drv: D12.5 (MISO\Res), D13.5 (MISO\Res), D14.5 (MISO\Res), D15.5 (MISO\Res), D16.5 (MISO\Res), D17.5 (MISO\Res); also elsewhere on the board
/mosi_drv: D12.2 (MOSI\MS1), D13.2 (MOSI\MS1), D14.2 (MOSI\MS1), D15.2 (MOSI\MS1), D16.2 (MOSI\MS1), D17.2 (MOSI\MS1); also elsewhere on the board
/sck_drv: D12.3 (SCK\MS2), D13.3 (SCK\MS2), D14.3 (SCK\MS2), D15.3 (SCK\MS2), D16.3 (SCK\MS2), D17.3 (SCK\MS2); also elsewhere on the board
/stp_e0: D14.7 (Step); also elsewhere on the board
/stp_e1: D17.7 (Step); also elsewhere on the board
/stp_x: D12.7 (Step); also elsewhere on the board
/stp_y: D13.7 (Step); also elsewhere on the board
/stp_z0: D15.7 (Step); also elsewhere on the board
/stp_z1: D16.7 (Step); also elsewhere on the board
GND: C34.2, C35.2, C36.2, C37.2, C38.2, C39.2, D12.9 (Gnd), D12.15 (Gnd), D13.9 (Gnd), D13.15 (Gnd), D14.9 (Gnd), D14.15 (Gnd), D15.9 (Gnd), D15.15 (Gnd), D16.9 (Gnd), D16.15 (Gnd), D17.9 (Gnd), D17.15 (Gnd), R28.1, R29.1, R30.1, R31.1, R32.1, R33.1; also elsewhere on the board
unnamed: D12.6 (NC\Sleep), R28.2
unnamed: D12.11 (M1B), J30.4
unnamed: D12.12 (M1A), J30.3
unnamed: D12.13 (M2A), J30.2
unnamed: D12.14 (M2B), J30.1
unnamed: D13.6 (NC\Sleep), R29.2
unnamed: D13.11 (M1B), J31.4
unnamed: D13.12 (M1A), J31.3
unnamed: D13.13 (M2A), J31.2
unnamed: D13.14 (M2B), J31.1
unnamed: D14.6 (NC\Sleep), R30.2
unnamed: D14.11 (M1B), J32.4
unnamed: D14.12 (M1A), J32.3
unnamed: D14.13 (M2A), J32.2
unnamed: D14.14 (M2B), J32.1
unnamed: D15.6 (NC\Sleep), R31.2
unnamed: D15.11 (M1B), J33.4
unnamed: D15.12 (M1A), J33.3
unnamed: D15.13 (M2A), J33.2
unnamed: D15.14 (M2B), J33.1
unnamed: D16.6 (NC\Sleep), R32.2
unnamed: D16.11 (M1B), J34.4
unnamed: D16.12 (M1A), J34.3
unnamed: D16.13 (M2A), J34.2
unnamed: D16.14 (M2B), J34.1
unnamed: D17.6 (NC\Sleep), R33.2
unnamed: D17.11 (M1B), J35.4
unnamed: D17.12 (M1A), J35.3
unnamed: D17.13 (M2A), J35.2
unnamed: D17.14 (M2B), J35.1
VCC: C34.1, C35.1, C36.1, C37.1, C38.1, C39.1, D12.16 (Vpow), D13.16 (Vpow), D14.16 (Vpow), D15.16 (Vpow), D16.16 (Vpow), D17.16 (Vpow); also elsewhere on the board

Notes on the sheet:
Разъём шагового двигателя 17HS4401

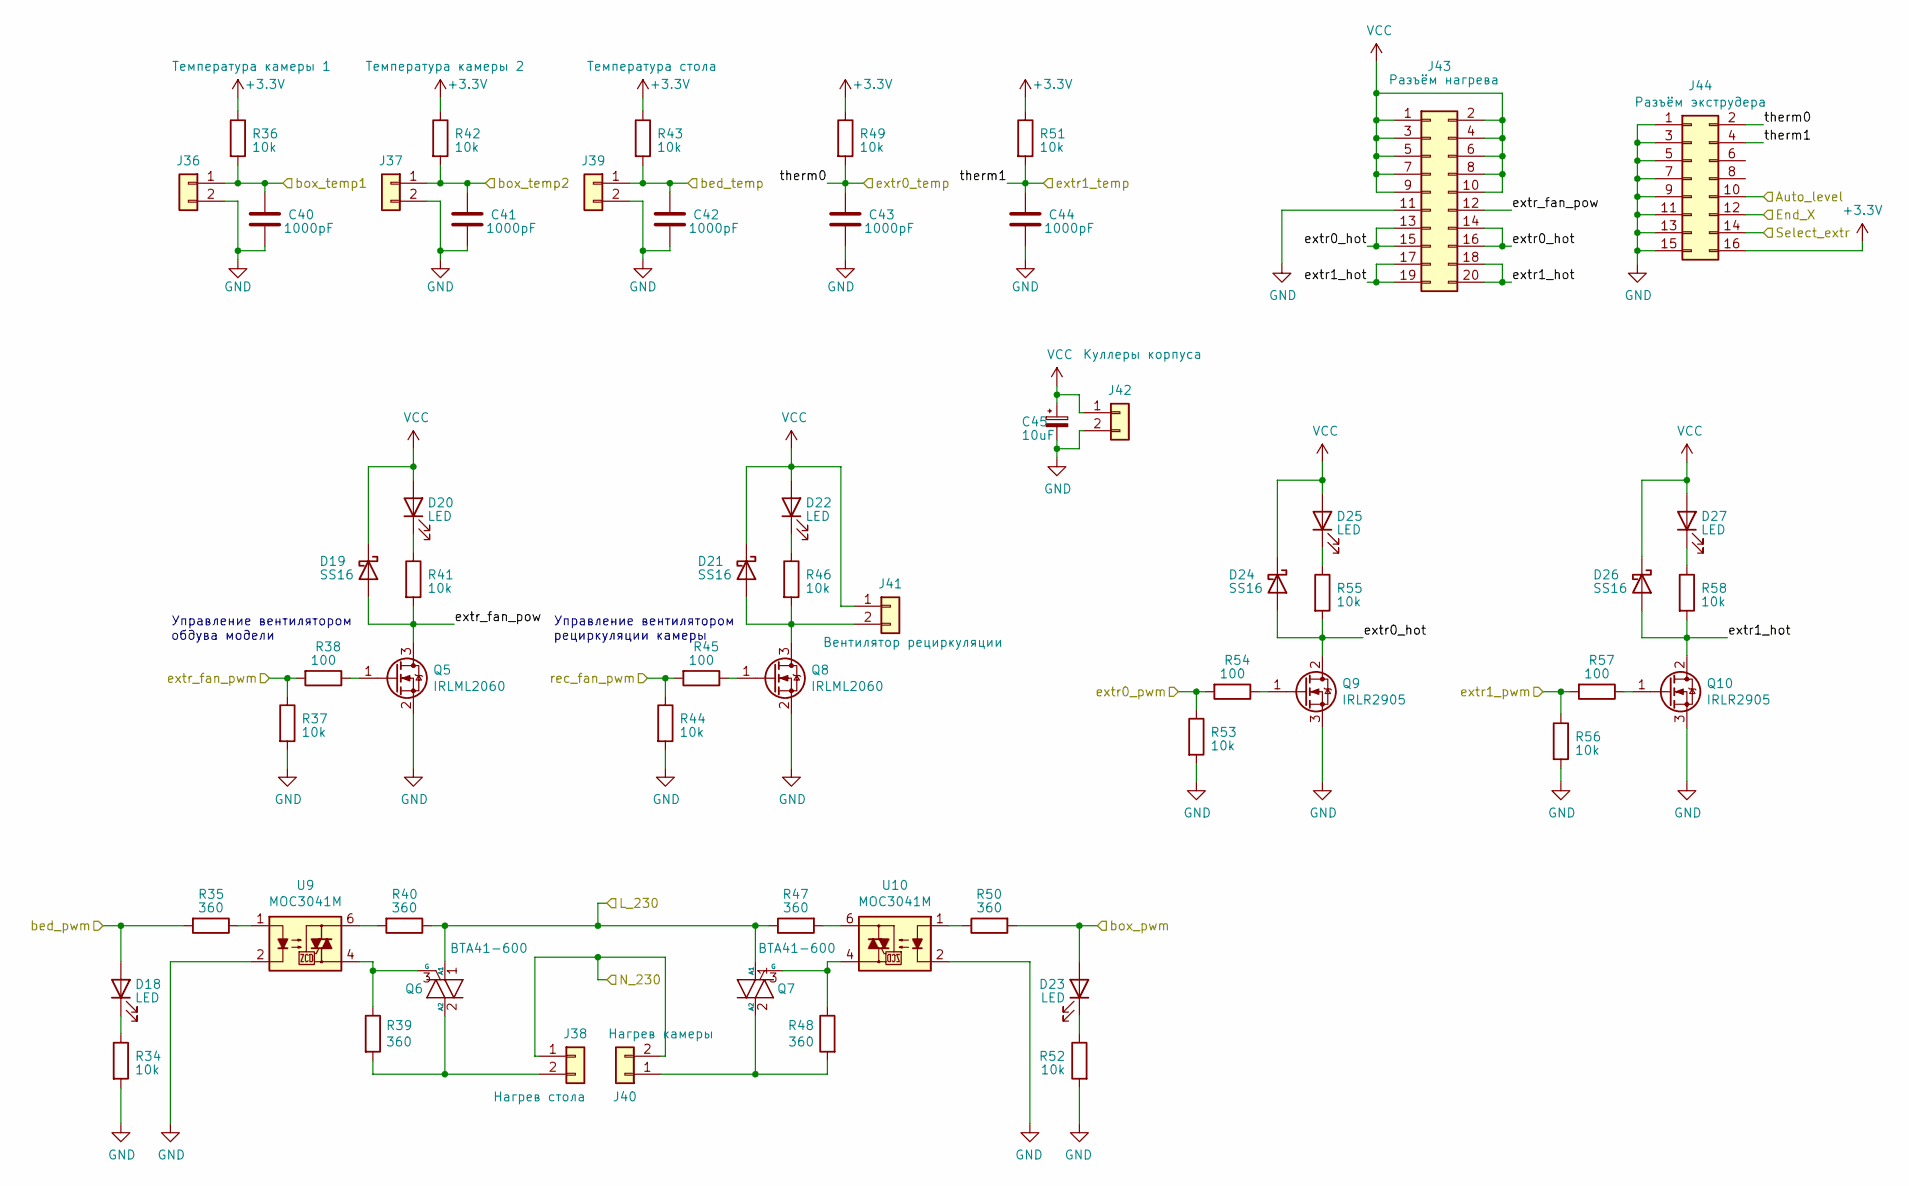
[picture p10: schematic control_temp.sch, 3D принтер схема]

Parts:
C40, C41, C42, C43, C44: 1000pF; C_0603_1608Metric
C45: 10uF; CP_EIA-6032-28_Kemet-C
D18, D20, D22, D23, D25, D27: LED; LED_1206_3216Metric
D19, D21, D24, D26: SS16; D_SMA
J36: Температура камеры 1; PhoenixContact_MCV_1,5_2-G-3.5_1x02_P3.50mm_Vertical
J37: Температура камеры 2; PhoenixContact_MCV_1,5_2-G-3.5_1x02_P3.50mm_Vertical
J38: Нагрев стола; PhoenixContact_MCV_1,5_2-G-3.5_1x02_P3.50mm_Vertical
J39: Температура стола; PhoenixContact_MCV_1,5_2-G-3.5_1x02_P3.50mm_Vertical
J40: Нагрев камеры; PhoenixContact_MCV_1,5_2-G-3.5_1x02_P3.50mm_Vertical
J41: Вентилятор рециркуляции; PhoenixContact_MCV_1,5_2-G-3.5_1x02_P3.50mm_Vertical
J42: Куллеры корпуса; PhoenixContact_MCV_1,5_2-G-3.5_1x02_P3.50mm_Vertical
J43: Разъём нагрева; IDC-Header_2x10_P2.54mm_Vertical
J44: Разъём экструдера; IDC-Header_2x08_P2.54mm_Vertical
Q5, Q8: IRLML2060; SOT-23
Q6, Q7: BTA41-600; TOP3
Q9, Q10: IRLR2905; TO-252-2
R34, R36, R37, R41, R42, R43, R44, R46, R49, R51, R52, R53, R55, R56, R58: 10k; R_0603_1608Metric
R35, R50: 360; R_0603_1608Metric
R38, R45, R54, R57: 100; R_0603_1608Metric
R39, R40, R47, R48: 360; R_1206_3216Metric
U9, U10: MOC3041M; DIP-6_W7.62mm

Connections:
+3V3: J44.16, R36.1, R42.1, R43.1, R49.1, R51.1; also elsewhere on the board
/Auto_level: J44.10; also elsewhere on the board
/L_230: Q6.1 (A1), Q7.1 (A1), R40.1, R47.1; also elsewhere on the board
/N_230: J38.1, J40.2; also elsewhere on the board
/X_endstop: J44.12; also elsewhere on the board
/bed_pwm: D18.2 (A), R35.2; also elsewhere on the board
/bed_temp: C42.1, J39.1, R43.2; also elsewhere on the board
/box_pwm: D23.2 (A), R50.2; also elsewhere on the board
/box_temp1: C40.1, J36.1, R36.2; also elsewhere on the board
/box_temp2: C41.1, J37.1, R42.2; also elsewhere on the board
/control_temp/extr0_hot: D24.2 (A), J43.13, J43.14, J43.15, J43.16, Q9.2 (D), R55.2
/control_temp/extr1_hot: D26.2 (A), J43.17, J43.18, J43.19, J43.20, Q10.2 (D), R58.2
/control_temp/extr_fan_pow: D19.2 (A), J43.12, Q5.3 (D), R41.2
/extr0_pwm: R53.1, R54.2; also elsewhere on the board
/extr0_temp: C43.1, J44.2, R49.2; also elsewhere on the board
/extr1_pwm: R56.1, R57.2; also elsewhere on the board
/extr1_temp: C44.1, J44.4, R51.2; also elsewhere on the board
/extr_fan_pwm: R37.1, R38.2; also elsewhere on the board
/rec_fan_pwm: R44.1, R45.2; also elsewhere on the board
GND: C40.2, C41.2, C42.2, C43.2, C44.2, C45.2, J36.2, J37.2, J39.2, J42.2, J43.11, J44.1, J44.3, J44.5, J44.7, J44.9, J44.11, J44.13, J44.15, Q5.2 (S), Q8.2 (S), Q9.3 (S), Q10.3 (S), R34.2, R37.2, R44.2, R52.2, R53.2, R56.2, U9.2, U10.2; also elsewhere on the board
unnamed: D18.1 (K), R34.1
unnamed: D20.1 (K), R41.1
unnamed: D21.2 (A), J41.2, Q8.3 (D), R46.2
unnamed: D22.1 (K), R46.1
unnamed: D23.1 (K), R52.1
unnamed: D25.1 (K), R55.1
unnamed: D27.1 (K), R58.1
unnamed: J38.2, Q6.2 (A2), R39.2
unnamed: J40.1, Q7.2 (A2), R48.2
unnamed: Q5.1 (G), R38.1
unnamed: Q6.3 (G), R39.1, U9.4
unnamed: Q7.3 (G), R48.1, U10.4
unnamed: Q8.1 (G), R45.1
unnamed: Q9.1 (G), R54.1
unnamed: Q10.1 (G), R57.1
unnamed: R35.1, U9.1
unnamed: R40.2, U9.6
unnamed: R47.2, U10.6
unnamed: R50.1, U10.1
VCC: C45.1, D19.1 (K), D20.2 (A), D21.1 (K), D22.2 (A), D24.1 (K), D25.2 (A), D26.1 (K), D27.2 (A), J41.1, J42.1, J43.1, J43.2, J43.3, J43.4, J43.5, J43.6, J43.7, J43.8, J43.9, J43.10; also elsewhere on the board

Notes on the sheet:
Управление вентилятором обдува модели
Управление вентилятором рециркуляции камеры

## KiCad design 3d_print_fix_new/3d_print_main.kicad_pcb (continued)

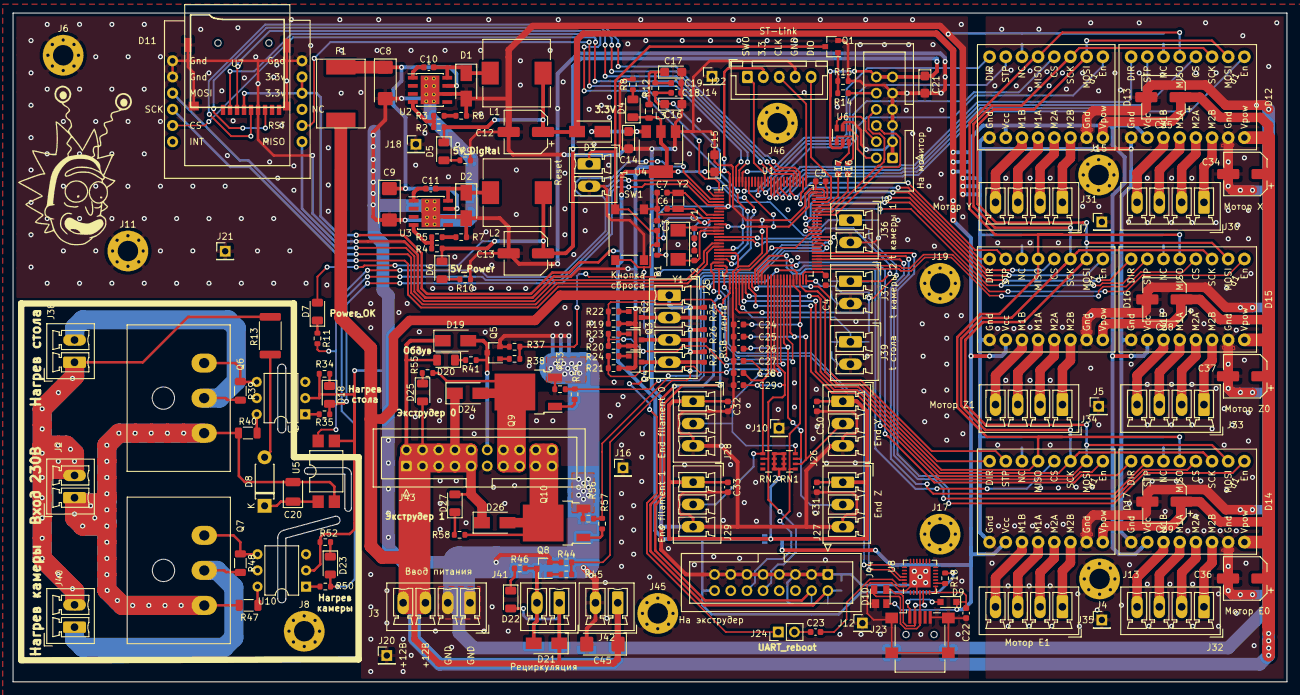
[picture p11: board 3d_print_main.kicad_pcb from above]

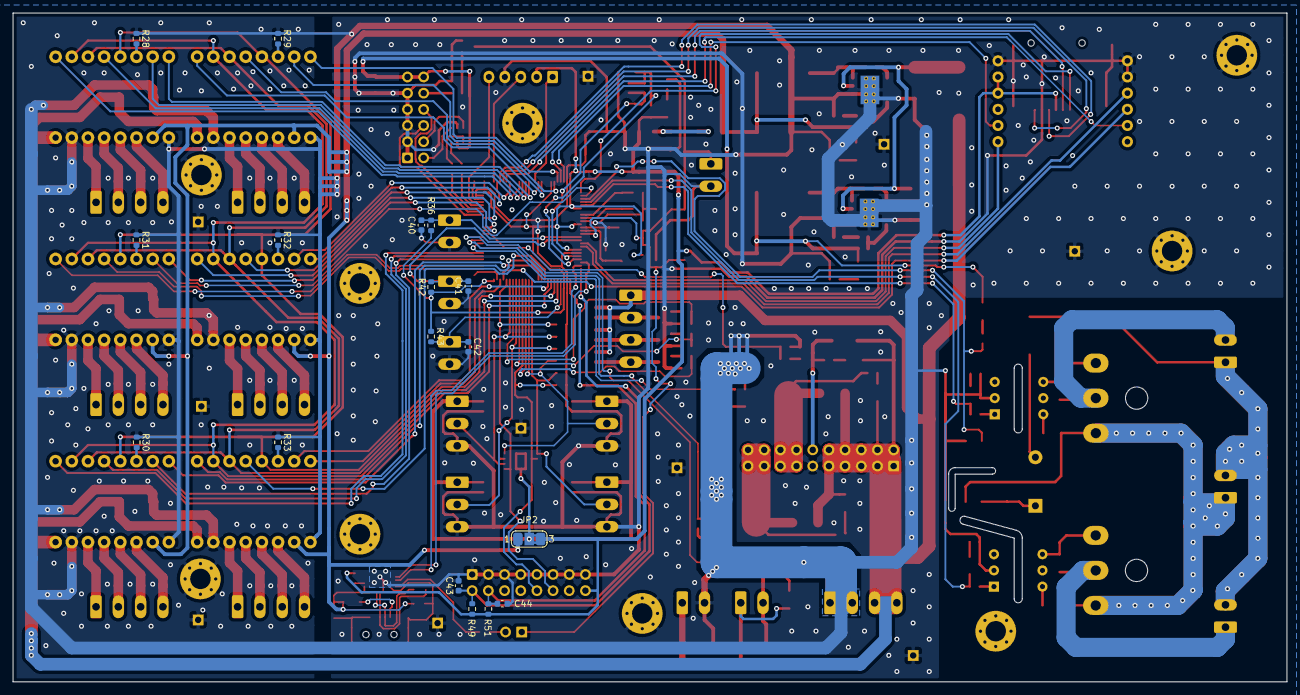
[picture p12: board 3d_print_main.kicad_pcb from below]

Board: 2 copper layers, 200.0 x 105.0 mm, 206 parts (17 on the bottom side), 169 nets.
